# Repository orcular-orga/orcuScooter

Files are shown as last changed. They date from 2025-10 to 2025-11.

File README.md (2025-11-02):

# orcuScooter

## 🛴♻️ Open Source Circular Scooter

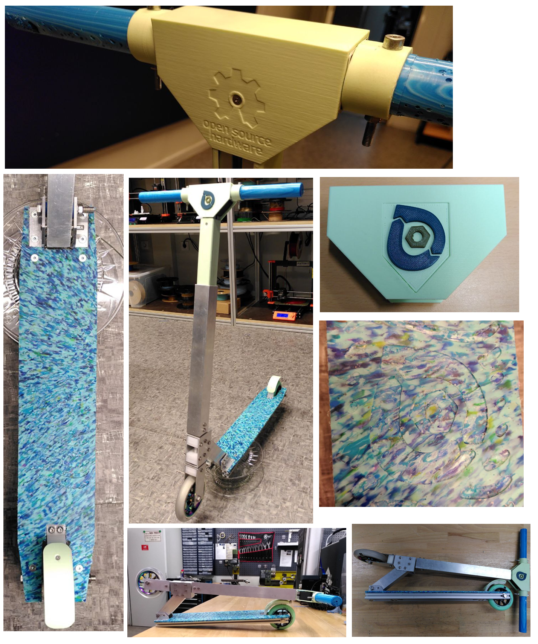
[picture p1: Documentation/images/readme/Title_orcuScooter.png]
 

The orcuScooter (short for "[Orcular](#%E2%84%B9%EF%B8%8F-about-the-orcular-project) Scooter") is an open-source kick scooter made from recycled plastics, aluminium and other parts. The main features are:
- Made from recycled plastics ([Precious Plastic](https://preciousplastic.com/) sheets)
- CNC milled parts
- 3D printed parts
- Circular design
  - Easy to repair & upgrade
  - Designed for disassembly
  - Most parts recyclebale
- [Open-source hardware](#-license)
- Designed in [FreeCAD](https://www.freecad.org/) (open-source software)
  - CAD file accessible in this repository
 
## 🏷️ Version
Recent version: 1.0 (released October 30th, 2025)

## 📐 CAD

This project has been designed in [FreeCAD](https://www.freecad.org/). You can find the CAD file [here](CAD)
 
## 🛠️ Building instructions
 
Here is all the information needed to manufacture and build an orcuScooter:

- 🛒 [Shopping list](Documentation/Shopping_list.md)
- ♻️ [Making sheets from recycled plastics](Documentation/Making_sheets.md)
- 🖨️ [3D printing](Documentation/3D_printing.md)
- ⚙️ CNC milling *(coming soon)*
- 🛠️ [Assembly](Documentation/Assembly.md)
- 🔼 Modding and upgrades *(coming soon)*

## 3D view

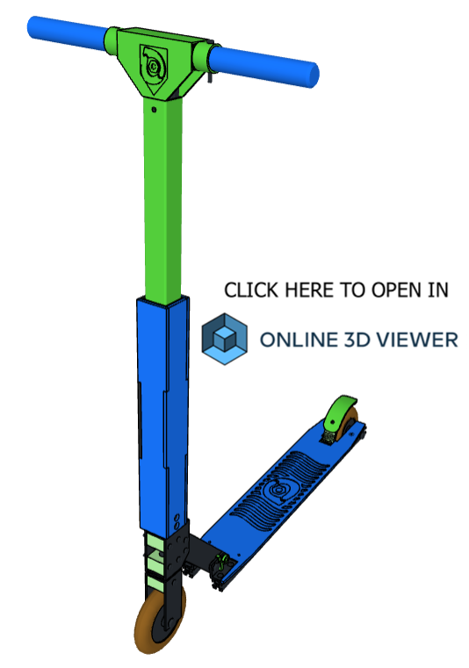
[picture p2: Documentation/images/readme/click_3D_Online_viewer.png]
[](https://3dviewer.net/embed.html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,-821.80037,1238.35295,82.32449,307.77471,405.61716,0.00000,-0.00000,1.00000,45.00000$projectionmode=perspective$envsettings=fishermans_bastion,off$backgroundcolor=255,255,255,255$defaultcolor=200,200,200$defaultlinecolor=100,100,100$edgesettings=on,0,0,0,84)

- It is best to open the view in a new tab (right-click on the image above -> Open link in new tab)
- Please be patient and wait about a minute to load the online 3D view

Controls:
- On computer: Use the left mouse button to rotate, the right mouse button to pan and the mouse wheel to zoom
- On smartphones: Swipe to rotate, use two fingers to zoom and pan 

- Alternative 3D view with more tools [here](https://3dviewer.net/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)
  - Click "Set Z axis as up vector" for better display a 
  - You can hide/show parts and groups on the left-hand side
  - For a complete view of the 3D file, download the [CAD file](CAD) and open it in [FreeCAD](https://www.freecad.org/)

## ℹ️ About the Orcular project
The orcuScooter is part of the Orcular project - https://www.orcular.org

"Orcular" stands for **O**pen Source + Ci**rcular** Economy

The project is about design concepts for locally recyclable products - for a constantly growing open source product library and the development of inner-city production.

Most components can be recycled into new parts - all within one city.
Recyclable plastic parts from the laser cutter, 3D printer and CNC mill, supplemented by standard parts.

## 📜🔓 License

The orcuScooter hardware design, CAD files, BOM, and relative files are released under the following open source license:

- [CERN Open Hardware Licence Version 2 Weakly Reciprocal - CERN-OHL-W](https://cern-ohl.web.cern.ch/)

The orcuScooter documentation, assembly manual, pictures and presentation text of this repository are released under the following license:

- [Creative-Commons-Attribution-ShareAlike 4.0 International - CC BY-SA 4.0](http://creativecommons.org/licenses/by-sa/4.0/)

**Author:** Oskar Lidtke, https://github.com/orcular-org/

<br />Except where otherwise noted, this work is licensed under a <a rel="license" href="http://creativecommons.org/licenses/by-sa/4.0/">Creative Commons Attribution-ShareAlike 4.0 International License (CC BY-SA 4.0)</a>.

See best practices for [attribution](https://wiki.creativecommons.org/wiki/Best_practices_for_attribution) and [marking your own work](https://wiki.creativecommons.org/wiki/Marking_your_work_with_a_CC_license) with a CC license.

<p align="left">
<i> <sub> Open Source Hardware logo, <a href="https://creativecommons.org/licenses/by-sa/4.0/">CC BY-SA</a> - <a href="https://oshwa.org/resources/open-source-hardware-logo/">Source</a> </sub></i>
</p>



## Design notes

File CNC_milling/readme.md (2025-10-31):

This folder contains the CNC milling vector graphics files. For CNC milling instructions, see the [documentation](../Documentation/Introduction.md), section **CNC milling**.

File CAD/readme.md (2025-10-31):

**Recent version: 1.0** - released on October 30, 2025.

The CAD model was designed in FreeCAD. You can download this free and open-source software on https://www.freecad.org

For modding instructions and changing parameters in the CAD file, see the [documentation](../Documentation/Introduction.md), section **Modding and upgrades**.

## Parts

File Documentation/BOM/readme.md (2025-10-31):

BOM / Shopping list

Can also be found here: [Google Docs Link](https://docs.google.com/spreadsheets/d/1hvMtBMdU-MjT3f36fKkWHgp-UORz1duzvwJJqe4S46w/edit?usp=drive_link)

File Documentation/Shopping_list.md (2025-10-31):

# Shopping list + bill of materials (BOM)

The shopping list / BOM can be found here [Google Docs Link](https://docs.google.com/spreadsheets/d/1hvMtBMdU-MjT3f36fKkWHgp-UORz1duzvwJJqe4S46w/edit?usp=drive_link)
or can be downloaded here: [Download BOM](BOM)

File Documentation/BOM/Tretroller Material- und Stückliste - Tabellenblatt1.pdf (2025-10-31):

## 🛠 Material- und Stückliste

Für einen (1)
Tretroller- Prototypen

Für zwei (2)
Prototypen
+ Puffer
Funktion | Material / Bauteil | Maße | Menge

Benötigte
Menge

Stück / Verkaufseinh.

Verkaufseinh.
bestellen | Link
🔲 Aluminium-Vierkantprofile, -Winkel und -Rundstäbe | L = 130 , da die Mindestlänge 50 mm beträgt, also 40 mm nicht möglich --> 130 mm bestellen und auseinandersägen
Fork | Vierkantprofil | 100x40x3 L=40 | 1 | 1 | https://www.metallparadies.de/alu-vierkantrohr.html
Bearing Box | Vierkantprofil | 80x40x3 L=58 | 1 | 2 | https://www.metallparadies.de/alu-vierkantrohr.html
Cross Connection | Vierkantprofil | 40x30x4 L=190 | 1 | 2 | https://www.metallparadies.de/alu-vierkantrohr.html
Gehrungswinkel: 45 ° und 38 °
Axle | Rundstab | D=12 | L=147 | 1 | 2 | https://www.metallparadies.de/alu-vollrohr.html
Handle Bar Bottom | Vierkantprofil | 40x40x2 L=373 | 1 | 2 | https://www.metallparadies.de/alu-vierkantrohr.html
Angle | Winkel | 30x20x4 L=50 | 2 | 4 | https://www.metallparadies.de/aluwinkel.html
Bestellwert metallparadies | Warenwert | 72,77€
Versandkosten | 10,77€

### ✖ Konstruktionsprofile + Winkel + Nutensteine (Muttern für T-Nuten)

Handle Bar Top | Konstruktionsprofil | 30x30 L=364 | 1 | 2 | https://www.maunsystem.de/profil-6-30x30-natur/pi-3010-sz#ncfg=364
Handle Bar Horizontal | Konstruktionsprofil | 30x30 L=112 | 1 | 2 | https://www.maunsystem.de/profil-6-30x30-natur/pi-3010-sz#ncfg=112
Frame Base | Konstruktionsprofil | 20x20 L=504 | 2 | 4 | https://www.maunsystem.de/profil-5-20x20-natur/pi-4030-sz#ncfg=504
Frame Connectors | Konstruktionsprofil | 20x20 L=41 | 2 | 4 | https://www.maunsystem.de/profil-5-20x20-natur/pi-4030-sz#ncfg=41
Frame | Winkelsatz 20 x 20 | | | 4 | 8 | https://www.maunsystem.de/winkelsatz-5-20x20/zi-4040
Handle Bar Top | Winkelsatz 30 x 30 | | | 2 | 4 | https://www.maunsystem.de/winkelsatz-6-30x30/zi-3070
Handle Bar Top <-> Flügelschraube | Nutenstein | M5 | | 1 | 2 | https://www.maunsystem.de/nutenstein-5-st-m5-verzinkt/ni-4035
Handle Bar Top <-> Begrenzung | Nutenstein | M5 | | 1 | 2 | https://www.maunsystem.de/nutenstein-5-st-m5-verzinkt/ni-4035
Bestellwert maunsystem | Warenwert | 134,18€
Versandkosten | 59,95€

### 🔩 Schrauben + Muttern + Unterlegscheiben

Hinweis: Alle Schrauben, Muttern, Unterlegscheiben möglichst aus Edelstahl, da Regen/Feuchtigkeit ausgesetzt (Korrosionsschutz) - Festigkeitsklasse A2 bevorzugt, da günstiger und ausreichende Festigkeit
Rear Wheel (Axle) | Sechskantschraube, Teilgewinde | M8 x 95 | 1 | https://www.schraubenking-shop.de/M8-x-95mm-Sechskantschrauben-DIN931-Teilgewinde-Edelstahl-A2-P005472
| Mutter | M8 | 1 | https://www.schraubenking-shop.de/M8-Sechskantmuttern-DIN934-Edelstahl-A2-P000451
| Unterlegscheibe (Außen-D = 20) | M8 | 2 | https://www.schraubenking-shop.de/84-x-20mm-Kotfluegelscheiben-Edelstahl-A2-P009141
Angle <-> Frame | Senkkopfschraube | M5 x 30 | 4 | https://www.schraubenking-shop.de/M5-x-30mm-Senkschrauben-ISO10642-Edelstahl-A2-P001361
| Mutter | M5 | 4 | https://www.schraubenking-shop.de/M5-Sechskantmuttern-DIN934-Edelstahl-A2-P000449
| Unterlegscheibe (Außen-D = 20) | M5 | 4 | https://www.schraubenking-shop.de/53-x-20mm-Kotfluegelscheiben-Edelstahl-A2-P008767
Angle <-> Cross Connection | Sechskantschraube, Teilgewinde | M8 x 65 | 1 | https://www.schraubenking-shop.de/M8-x-65mm-Sechskantschrauben-DIN931-Teilgewinde-Edelstahl-A2-P002677
| Mutter | M8 | 1 | https://www.schraubenking-shop.de/M8-Sechskantmuttern-DIN934-Edelstahl-A2-P000451
| Unterlegscheibe | M8 | 2 | https://www.schraubenking-shop.de/84mm-Unterlegscheiben-DIN125-Edelstahl-A2-P000475
Bearing Box <-> Cross Connection | Sechskantschraube, Teilgewinde | M5 x 50 | 2 | https://www.schraubenking-shop.de/M5-x-50mm-Sechskantschrauben-DIN931-Teilgewinde-Edelstahl-A2-P000277
| Mutter | M5 | 2 | https://www.schraubenking-shop.de/M5-Sechskantmuttern-DIN934-Edelstahl-A2-P000449
| Unterlegscheibe | M5 | 4 | https://www.schraubenking-shop.de/53mm-Unterlegscheiben-DIN125-Edelstahl-A2-P000036
Bearing Box <-> Bearing Housing | Sechskantschraube, Teilgewinde | M5 x 50 | 4 | https://www.schraubenking-shop.de/M5-x-50mm-Sechskantschrauben-DIN931-Teilgewinde-Edelstahl-A2-P000277
| Mutter | M5 | 4 | https://www.schraubenking-shop.de/M5-Sechskantmuttern-DIN934-Edelstahl-A2-P000449
| Unterlegscheibe | M5 | 8 | https://www.schraubenking-shop.de/53mm-Unterlegscheiben-DIN125-Edelstahl-A2-P000036
Fork <-> Axle | Sechskantschraube, Teilgewinde | M5 x 50 | 1 | https://www.schraubenking-shop.de/M5-x-50mm-Sechskantschrauben-DIN931-Teilgewinde-Edelstahl-A2-P000277
| Mutter | M5 | 1 | https://www.schraubenking-shop.de/M5-Sechskantmuttern-DIN934-Edelstahl-A2-P000449
| Unterlegscheibe | M5 | 2 | https://www.schraubenking-shop.de/53mm-Unterlegscheiben-DIN125-Edelstahl-A2-P000036
Front Wheel (Axle) | Sechskantschraube, Teilgewinde | M8 x 50 | 1 | https://www.schraubenking-shop.de/M8-x-50mm-Sechskantschrauben-DIN931-Teilgewinde-Edelstahl-A2-P005469
| Mutter | M8 | 1 | https://www.schraubenking-shop.de/M8-Sechskantmuttern-DIN934-Edelstahl-A2-P000451
| Unterlegscheibe | M8 | 2 | https://www.schraubenking-shop.de/84mm-Unterlegscheiben-DIN125-Edelstahl-A2-P000475
Handle Bar Bottom <-> Axle (+ Nylonschiene) | Sechskantschraube, Teilgewinde | M5 x 50 | 3 | https://www.schraubenking-shop.de/M5-x-50mm-Sechskantschrauben-DIN931-Teilgewinde-Edelstahl-A2-P000277

| Mutter | M5 | 3 | | | | | https://www.schraubenking-shop.de/M5-Sechskantmuttern-DIN934-Edelstahl-A2-P000449
| Unterlegscheibe | M5 | 4 | | | | | https://www.schraubenking-shop.de/53mm-Unterlegscheiben-DIN125-Edelstahl-A2-P000036
Arretierung höhenverstellbarer Lenker | Flügelschraube | M5 x 16 | 1 | | | | | https://www.schraubenking-shop.de/M5-x-16mm-Fluegelschrauben-amerik-Form-Edelstahl-A2-P005164
Schraube f. Nutenstein Begrenzung Lenkstange Linsenflachkopfschraube | M5 x 10 | 1 | https://www.schraubenking-shop.de/M5-x-10mm-Linsenflachkopfschraube-ISK-ISO7380-Edelstahl-A2-P004443
Begrenzung Nylonschiene oben + für Inserts | Senkschraube | M3 x 12 | 8 | | | | | https://www.schraubenking-shop.de/M3-x-12mm-Senkschrauben-ISO10642-Edelstahl-A2-P002506
| Mutter | M3 | 2 | | | | | https://www.schraubenking-shop.de/M3-Sechskantmuttern-DIN934-Edelstahl-A2-P000447

Sortiert nach Teiletyp:

Schrauben

Benötigte
Menge
| | | | | Stück / Verkaufseinh. | Verkaufseinh.
bestellen | Warenkorb
Rear Wheel (Axle) | Sechskantschraube, Teilgewinde | M8 x 95 | 1 | 2 | 1 | 2 | x | https://www.schraubenking-shop.de/M8-x-95mm-Sechskantschrauben-DIN931-Teilgewinde-Edelstahl-A2-P005472
Angle <-> Frame | Senkkopfschraube | M5 x 30 | 4 | 8 | 10 | 1 | x | https://www.schraubenking-shop.de/M5-x-30mm-Senkschrauben-ISO10642-Edelstahl-A2-P001361
Angle <-> Cross Connection | Sechskantschraube, Teilgewinde | M8 x 65 | 1 | 2 | 1 | 2 | x | https://www.schraubenking-shop.de/M8-x-65mm-Sechskantschrauben-DIN931-Teilgewinde-Edelstahl-A2-P002677
Bearing Box <-> Cross Connection | Sechskantschraube, Teilgewinde | M5 x 50 | 2 | 4 | | | | https://www.schraubenking-shop.de/M5-x-50mm-Sechskantschrauben-DIN931-Teilgewinde-Edelstahl-A2-P000277
Bearing Box <-> Bearing Housing | Sechskantschraube, Teilgewinde | M5 x 50 | 4 | 8 | | | | https://www.schraubenking-shop.de/M5-x-50mm-Sechskantschrauben-DIN931-Teilgewinde-Edelstahl-A2-P000277
Fork <-> Axle | Sechskantschraube, Teilgewinde | M5 x 50 | 1 | 2 | | | | https://www.schraubenking-shop.de/M5-x-50mm-Sechskantschrauben-DIN931-Teilgewinde-Edelstahl-A2-P000277
Handle Bar Bottom <-> Axle (+ Nylonschiene) | Sechskantschraube, Teilgewinde | M5 x 50 | 3 | 6 | | | | https://www.schraubenking-shop.de/M5-x-50mm-Sechskantschrauben-DIN931-Teilgewinde-Edelstahl-A2-P000277
Gesamt M5 x 50 | | | | 20 | 10 | 3 | x
Front Wheel (Axle) | Sechskantschraube, Teilgewinde | M8 x 50 | 1 | 2 | 1 | 2 | x | https://www.schraubenking-shop.de/M8-x-50mm-Sechskantschrauben-DIN931-Teilgewinde-Edelstahl-A2-P005469
Arretierung höhenverstellbarer Lenker | Flügelschraube | M5 x 16 | 1 | 2 | 1 | 2 | x | https://www.schraubenking-shop.de/M5-x-16mm-Fluegelschrauben-amerik-Form-Edelstahl-A2-P005164
Schraube f. Nutenstein Begrenzung Lenkstange Linsenflachkopfschraube | M5 x 10 | 1 | 2 | 10 | 1 | x | https://www.schraubenking-shop.de/M5-x-10mm-Linsenflachkopfschraube-ISK-ISO7380-Edelstahl-A2-P004443
Begrenzung Nylonschiene oben + für Inserts | Senkschraube | M3 x 12 | 8 | 16 | 100 | 1 | x | https://www.schraubenking-shop.de/M3-x-12mm-Senkschrauben-ISO10642-Edelstahl-A2-P002506

Muttern
| Mutter | M8 | 1 | 2 | | | | https://www.schraubenking-shop.de/M8-Sechskantmuttern-DIN934-Edelstahl-A2-P000451
| Mutter | M8 | 1 | 2 | | | | https://www.schraubenking-shop.de/M8-Sechskantmuttern-DIN934-Edelstahl-A2-P000451
| Mutter | M8 | 1 | 2 | | | | https://www.schraubenking-shop.de/M8-Sechskantmuttern-DIN934-Edelstahl-A2-P000451
Gesamt Muttern M8 | | | | 6 | 10 | 1 | x
| Mutter | M5 | 4 | 8 | | | | https://www.schraubenking-shop.de/M5-Sechskantmuttern-DIN934-Edelstahl-A2-P000449
| Mutter | M5 | 2 | 4 | | | | https://www.schraubenking-shop.de/M5-Sechskantmuttern-DIN934-Edelstahl-A2-P000449
| Mutter | M5 | 4 | 8 | | | | https://www.schraubenking-shop.de/M5-Sechskantmuttern-DIN934-Edelstahl-A2-P000449
| Mutter | M5 | 1 | 2 | | | | https://www.schraubenking-shop.de/M5-Sechskantmuttern-DIN934-Edelstahl-A2-P000449
| Mutter | M5 | 3 | 6 | | | | https://www.schraubenking-shop.de/M5-Sechskantmuttern-DIN934-Edelstahl-A2-P000449
Gesamt Muttern M5 | | | | 28 | 100 | 1 | x
Begrenzung Nylonschiene oben + für Inserts | Mutter | M3 | 2 | 4 | 100 | 1 | x | https://www.schraubenking-shop.de/M3-Sechskantmuttern-DIN934-Edelstahl-A2-P000447

Unterlegscheiben
| Unterlegscheibe (Außen-D = 20) | M8 | 2 | 4 | 10 | 1 | x | https://www.schraubenking-shop.de/84-x-20mm-Kotfluegelscheiben-Edelstahl-A2-P009141
| Unterlegscheibe (Außen-D = 20) | M5 | 4 | 8 | 10 | 1 | x | https://www.schraubenking-shop.de/53-x-20mm-Kotfluegelscheiben-Edelstahl-A2-P008767
| Unterlegscheibe (Außen-D = 16) | M8 | 2 | 4 | | | | https://www.schraubenking-shop.de/84mm-Unterlegscheiben-DIN125-Edelstahl-A2-P000475
| Unterlegscheibe (Außen-D = 16) | M8 | 2 | 4 | | | | https://www.schraubenking-shop.de/84mm-Unterlegscheiben-DIN125-Edelstahl-A2-P000475
Gesamt Unterlegscheibe M8 (Außen-D = 16) | | | | 8 | 100 | 1 | x
| Unterlegscheibe | M5 | 4 | 8 | | | | https://www.schraubenking-shop.de/53mm-Unterlegscheiben-DIN125-Edelstahl-A2-P000036
| Unterlegscheibe | M5 | 8 | 16 | | | | https://www.schraubenking-shop.de/53mm-Unterlegscheiben-DIN125-Edelstahl-A2-P000036
| Unterlegscheibe | M5 | 2 | 4 | | | | https://www.schraubenking-shop.de/53mm-Unterlegscheiben-DIN125-Edelstahl-A2-P000036
| Unterlegscheibe | M5 | 4 | 8 | | | | https://www.schraubenking-shop.de/53mm-Unterlegscheiben-DIN125-Edelstahl-A2-P000036

Gesamt Unterlegscheibe M5 | 36 | 100 | 1 | x
Bestellwert schraubenking | Warenwert | 18,38€
| Versandkosten | 5,90€

### ⚪🔩 Bolzen

Anlge <-> Cross Connection | Bolzen mit Kopf | 6 x 50 (6 x 48) | 1 | 3 | https://www.bootspunkt.de/steckbolzen-va-6x48-mm/ya-00-53102-0
Bestellwert bootspunkt | Warenwert | 2,55€
Versandkosten | 7,95€

### 🧵🔩 3D-Druck-Filament + Gewindeeinsätze zum Einschmelzen (Inserts)

| Nylon PA12 (750 g) | | 1 | 1 | https://www.reichelt.com/de/de/shop/produkt/filament_nylon_pa12_natural_1_75_mm_0_75_kg-405785
| PLA (1000 g) | | 1 | 1 | https://www.reichelt.de/de/de/shop/produkt/filament_panchroma_pla_matte_pastel_mint_1_75_mm_1_kg-405590
| Gewindeeinsatz zum Einschmelzen | M3 x 4 | 8 | 1 | https://www.reichelt.de/de/de/shop/produkt/3d_druck_gewindeeinsaetze_m3x4_short_100_stueck-332214
Bestellwert reichelt | Warenwert | 77,88€
Versandkosten | 5,95€

### 🍩 Kugellager

Lagerung Lenkachse | Schrägkugellager 7201 B offen TN | 12x32x10 mm | 2 | 4 | https://www.kugellager-express.de/schraegkugellager-7201-b-tn-offen-12x32x10-mm
Bestellwert kugellager-express | Warenwert | 18,61€
Versandkosten | 2,49€

### 🛒🛞 Kaufteile / Sonstige Teile

Front Wheel | Rolle | D=120 | 1 | 2 | https://angebot.decathlon.de/product/328632?modelId=8603756
Rear Wheel | Rolle | D=100 | 1 | 2 | https://angebot.decathlon.de/product/311734?modelId=8647663
Front + Rear Wheel (Eigenbau) | ABEC-5 Kugellager 2er Pack | | 2 | 2 | https://angebot.decathlon.de/product/312948?modelId=8575697
Bestellwert Decathlon | Warenwert | 75,94€
Versandkosten unbekannt
SUMME | 493,32 €

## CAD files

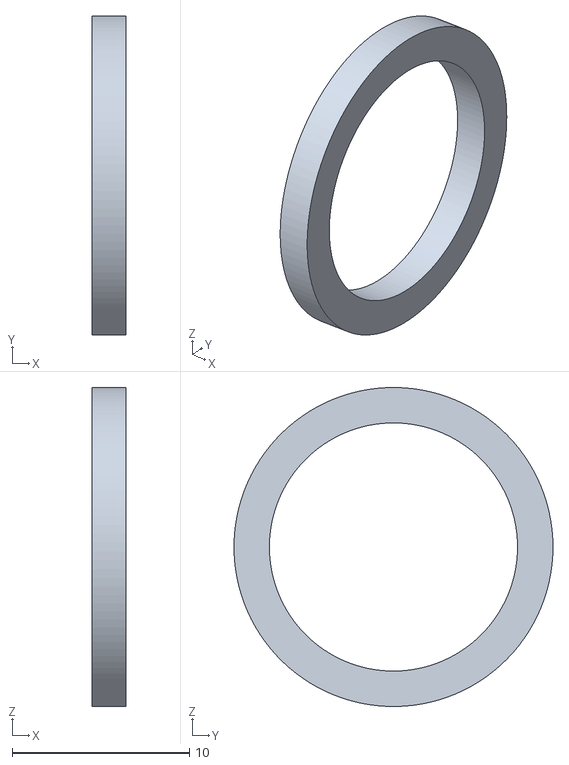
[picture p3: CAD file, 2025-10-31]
3D_printing/Nylon_(PA12)/3DP_Spacer_Cross_Connection_1,9.stl
1.90 x 18.0 x 18.0

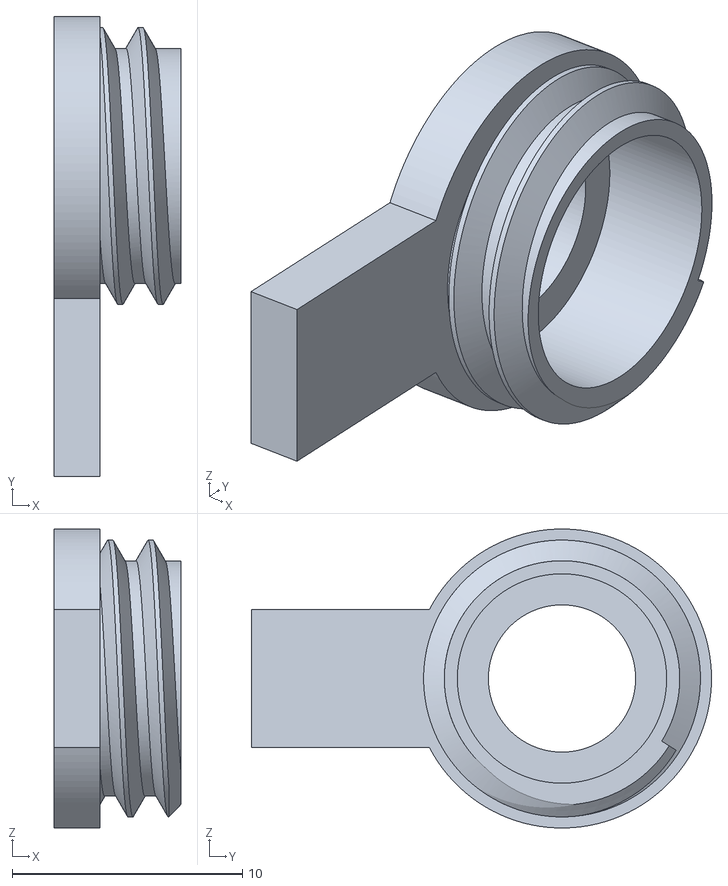
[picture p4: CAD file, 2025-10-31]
3D_printing/PLA/Cut.stl
5.50 x 20.0 x 13.0

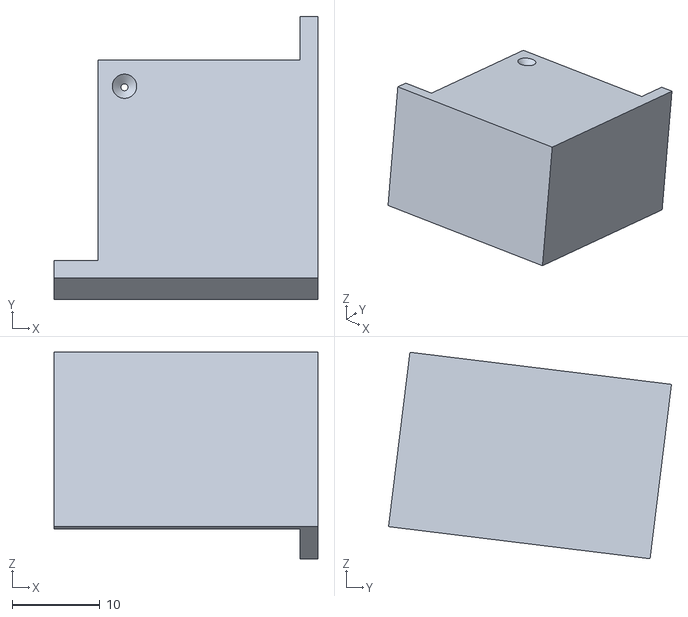
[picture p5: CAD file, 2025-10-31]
3D_printing/Templates_(PLA)/2-2_Drill_Guide.stl
30.0 x 32.2 x 23.5

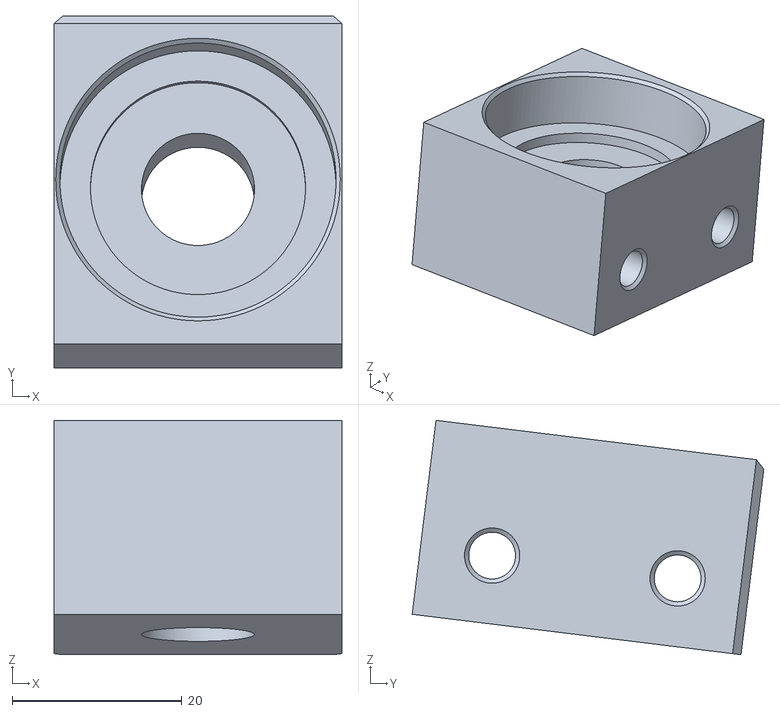
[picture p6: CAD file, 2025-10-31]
3D_printing/Nylon_(PA12)/3DP_Bearing_housing.stl
33.9 x 41.4 x 27.6

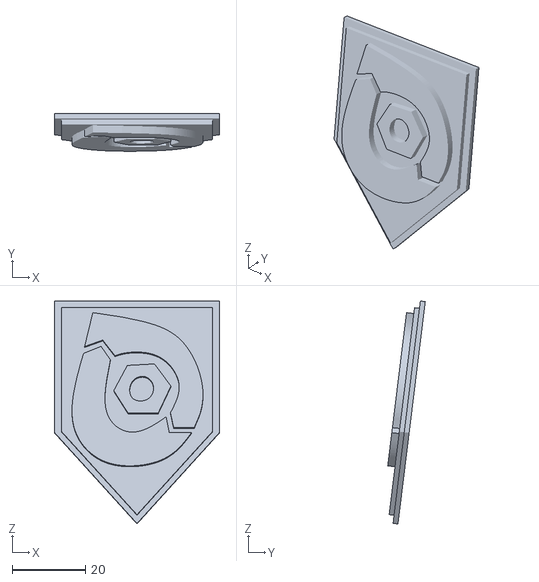
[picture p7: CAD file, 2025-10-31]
3D_printing/PLA/3DP_Logo_Orcular.stl
45.0 x 10.2 x 60.7

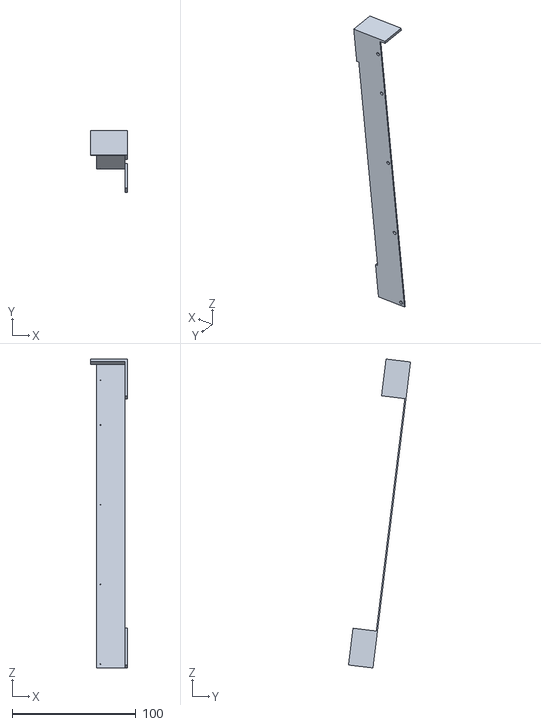
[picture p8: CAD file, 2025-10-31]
3D_printing/Templates_(PLA)/5-2_Drill_Guide.stl
30.0 x 50.3 x 250.1

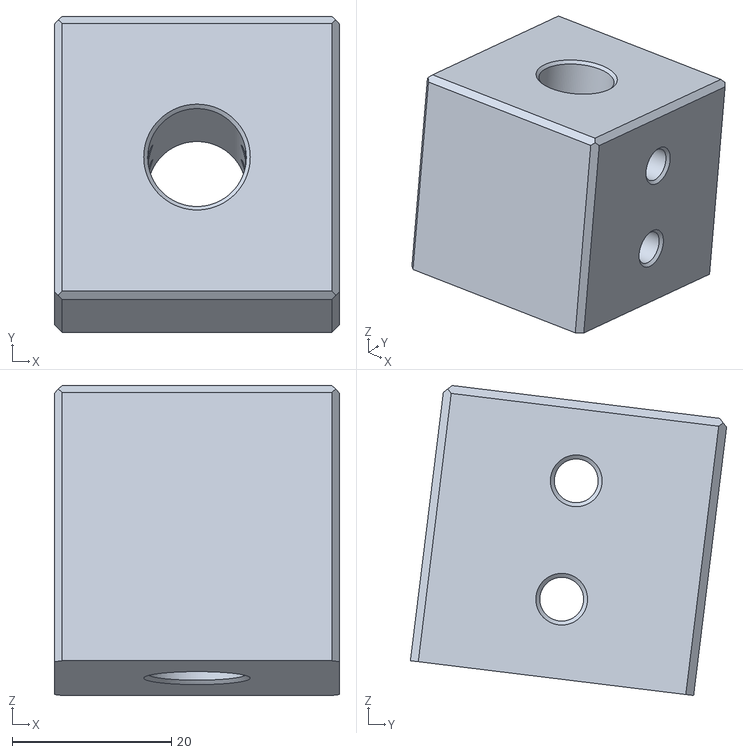
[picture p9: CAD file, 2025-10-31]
3D_printing/Nylon_(PA12)/3DP_Connector_Handle_Bar_Bottom+Axle.stl
35.9 x 39.8 x 39.0

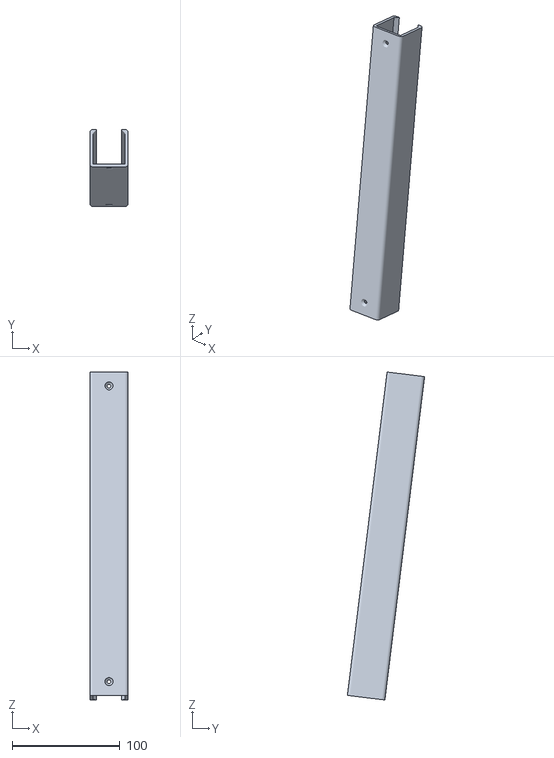
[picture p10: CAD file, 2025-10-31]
3D_printing/PLA/3DP_Case.stl
35.8 x 71.9 x 305.0

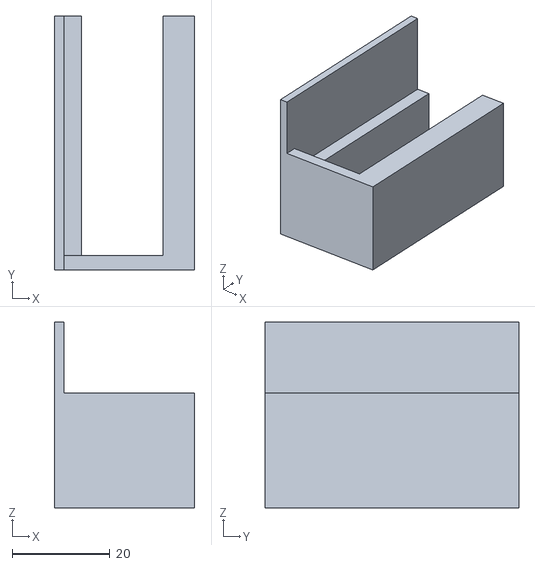
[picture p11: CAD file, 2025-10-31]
3D_printing/Templates_(PLA)/7-3_Drill_Guide.stl
28.7 x 52.0 x 38.0

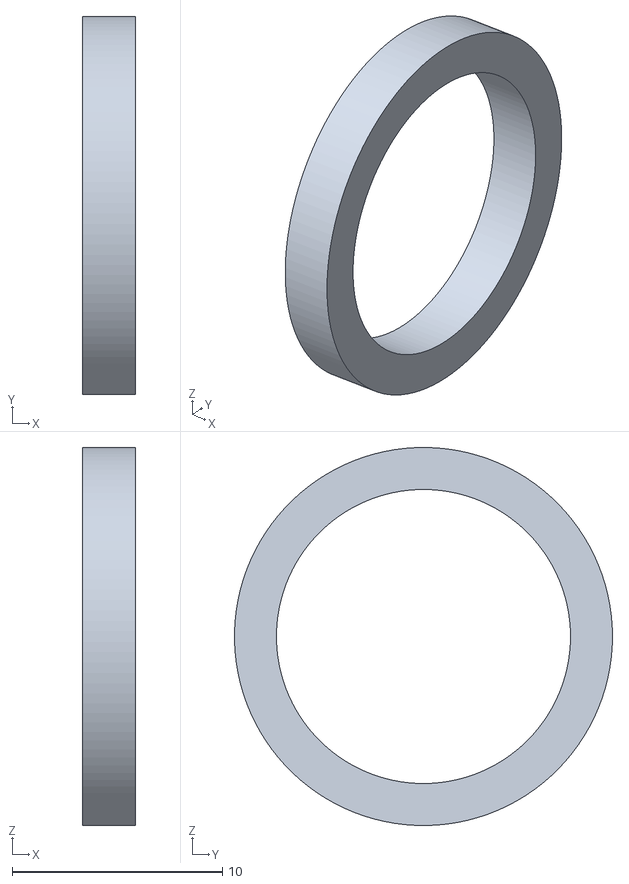
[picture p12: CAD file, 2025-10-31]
3D_printing/Nylon_(PA12)/3DP_Spacer_Cross_Connection_2,5.stl
2.50 x 18.0 x 18.0

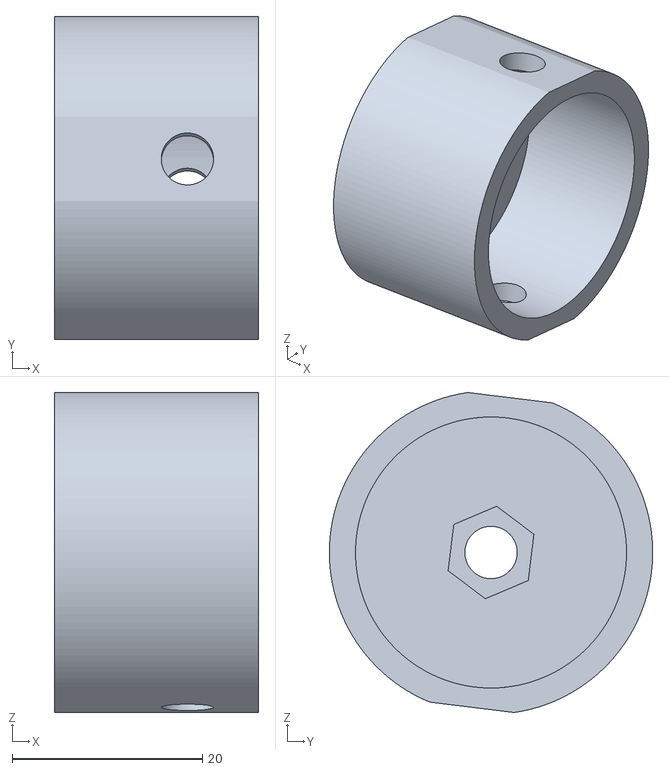
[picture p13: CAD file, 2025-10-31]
3D_printing/PLA/3DP_Handle_Adapter.stl
21.5 x 34.0 x 33.6

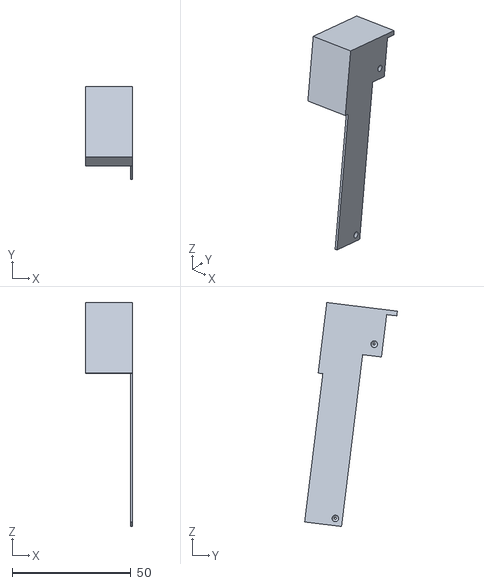
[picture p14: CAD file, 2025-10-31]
3D_printing/Templates_(PLA)/2-1_Drill_Guide.stl
20.0 x 39.1 x 94.5

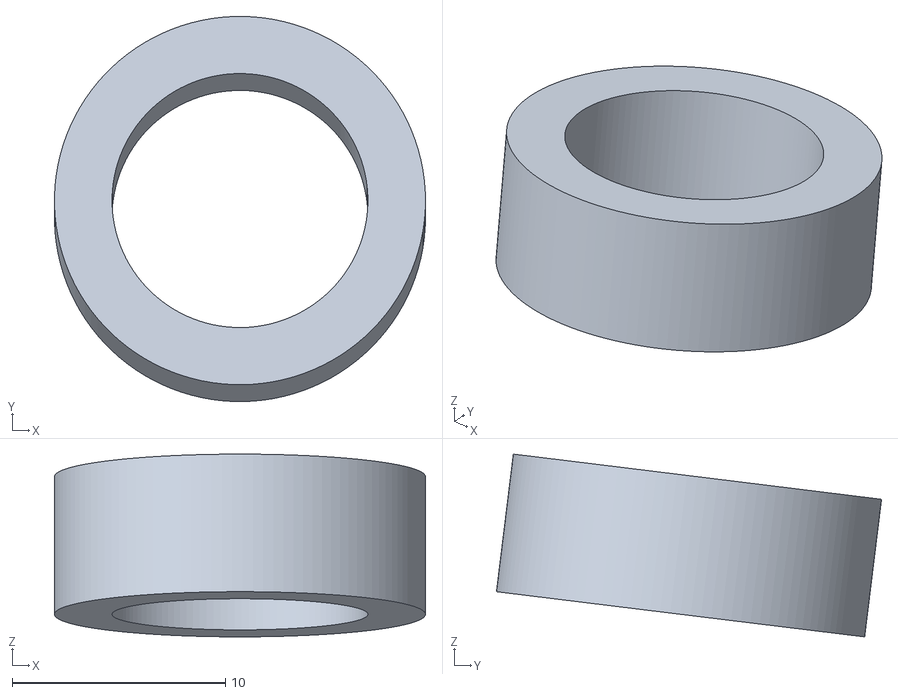
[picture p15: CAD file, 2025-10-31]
3D_printing/Nylon_(PA12)/3DP_Spacer_Handle_Bar_Bottom.stl
17.4 x 18.1 x 8.57

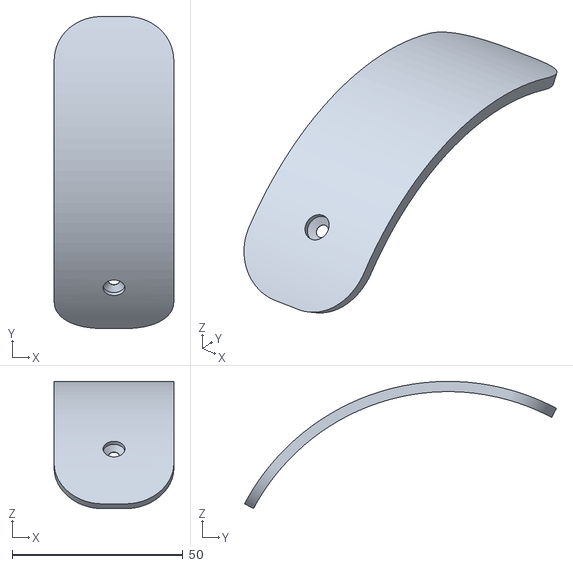
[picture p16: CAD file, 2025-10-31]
3D_printing/PLA/3DP_Brake_Cover.stl
35.0 x 91.3 x 37.2

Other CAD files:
3D_printing/Templates_(PLA)/7-2_Drill_Guide.stl
3D_printing/Nylon_(PA12)/3DP_Plain_bearing_rotation.stl
3D_printing/PLA/3DP_Front_Cover.stl
3D_printing/Templates_(PLA)/5-1_Drill_Guide.stl
3D_printing/Nylon_(PA12)/3DP_Brake.stl
3D_printing/Nylon_(PA12)/3DP_Connector_Fork.stl
3D_printing/Nylon_(PA12)/3DP_Nylon-Schiene.stl
3D_printing/Nylon_(PA12)/3DP_Spacer_Bearing_Box.stl
3D_printing/Nylon_(PA12)/3DP_Spacer_Fork.stl
3D_printing/Nylon_(PA12)/3DP_Spacer_Front_Wheel.stl
3D_printing/Nylon_(PA12)/3DP_Spacer_Rear_Wheel.stl
3D_printing/PLA/Deckel_real.stl
3D_printing/PLA/Klammer.stl
3D_printing/Templates_(PLA)/7-1a_Drill_Guide.stl
3D_printing/Templates_(PLA)/7-1b_Drill_Guide.stl
3D_printing/Templates_(PLA)/7-4_Drill_Guide.stl
3D_printing/Templates_(PLA)/7-5_Drill_Guide.stl

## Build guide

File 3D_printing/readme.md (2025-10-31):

This folder contains all 3D printing STL files. For printing instructions, see the [documentation](../Documentation/Introduction.md), section [3D printing](../Documentation/3D_printing.md).

You can click on any STL file to see a 3D view (GitHub feature).

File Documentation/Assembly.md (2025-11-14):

# Assembly

## Outline

💡ℹ️ You can find an outline (table of contents) in the upper right corner of this GitHub file and expand it by clicking on the icon. Click on the titles to jump to the corresponding section.

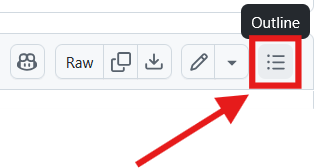
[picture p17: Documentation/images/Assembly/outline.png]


## Part list

Please check the part list in the [BOM section](Shopping_list.md)

## Tool list

Check that you have all the tools you need:

- A set of screw drivers and wrenches for hexagon screws (M3, M5 and M8)
- A set of allen keys
- Pliers

## Assembly

The assembly instructions are divided into several modules. These do not necessarily have to be assembled in the order listed below. Several people can also work on different modules at the same time. At the end, all modules must be assembled together.

## 1. Frame

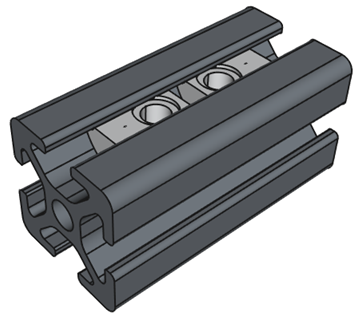
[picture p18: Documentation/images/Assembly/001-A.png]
<table> <tr> <td>  </td> <td> <ul>
        <li>Insert 2 t-nuts (M5) in one of the t-slot profiles (length 41 mm). You will need them later to assemble the brake.</li>
</table>

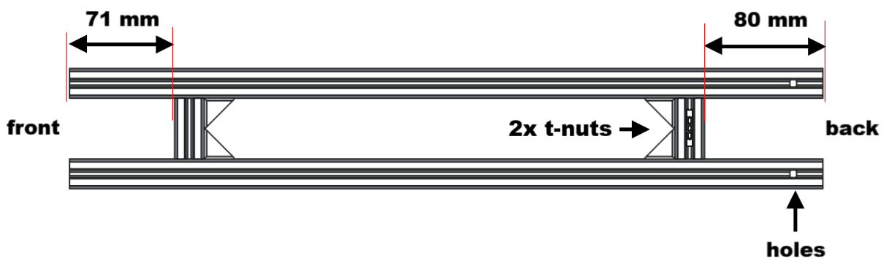
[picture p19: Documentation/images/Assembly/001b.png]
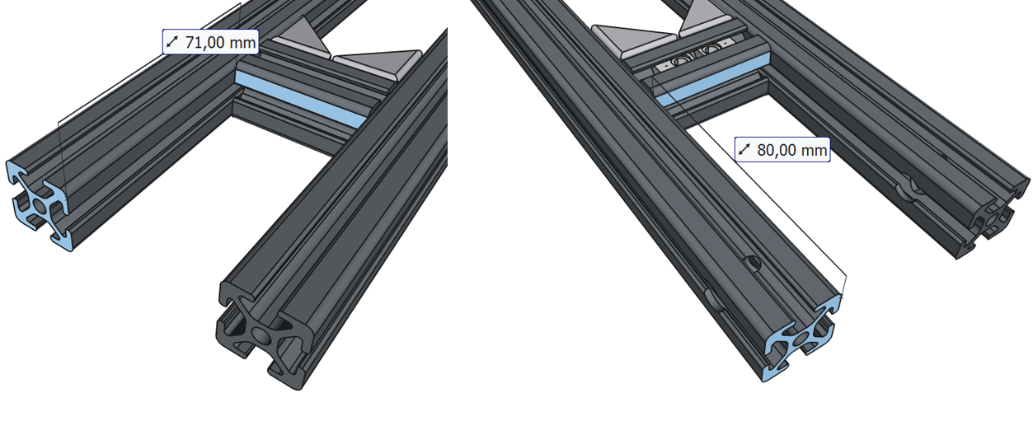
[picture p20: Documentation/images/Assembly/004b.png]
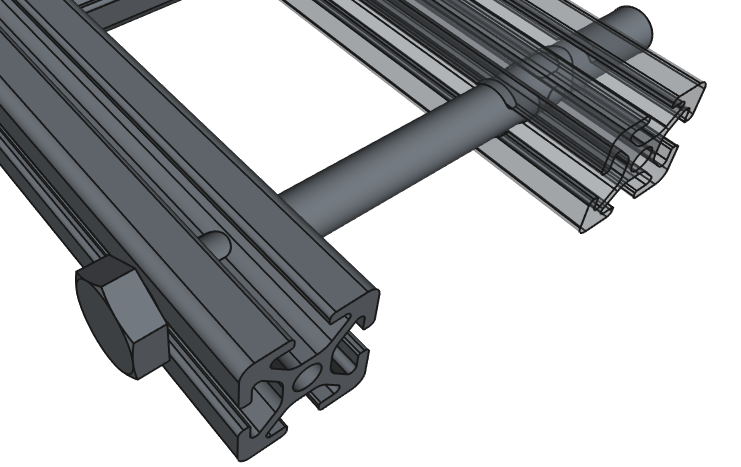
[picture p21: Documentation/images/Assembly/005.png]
<table> <tr> <td>  <br>  <br> </td> <td> <ul>
        <li>Assamble the following 20x20 t-slot profiles:
          <ul>
            <li>length 509 mm (2 pieces)</li>
            <li>length 41 mm (2 pieces)</li>
          </ul>
        </li>
        <li>Use four 20x20 angles for mounting</li>
        <li>For each angle, you will need 2x M5 screws and 2x t-nuts</li>
        <li>Make sure to move the 41-mm-profiles to the right position (80 mm for the back part, 71 mm for the front part)</li>
        <li>Make sure to put the part with the 2 t-nuts (for the brake) in the back part of the frame (with a distance 80 mm)</li>
        <li>Make sure that the drilled holes are in the back</li>
        <li>Make sure that everything is parallel and at right angles</li>
        <li>Insert the M8 x 95 screw through the holes and make sure that it fits well</li>
        <li>Do not fasten the screw yet. If the screw fits, remove it again. The rear wheel will be mounted later.</li>
      </ul> </td> </tr> </table>

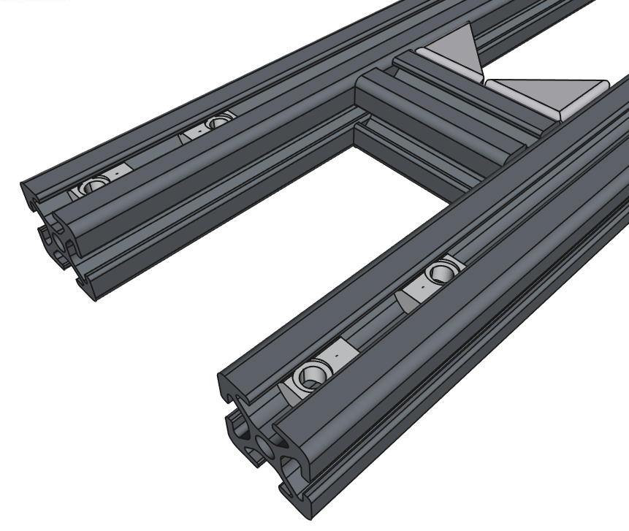
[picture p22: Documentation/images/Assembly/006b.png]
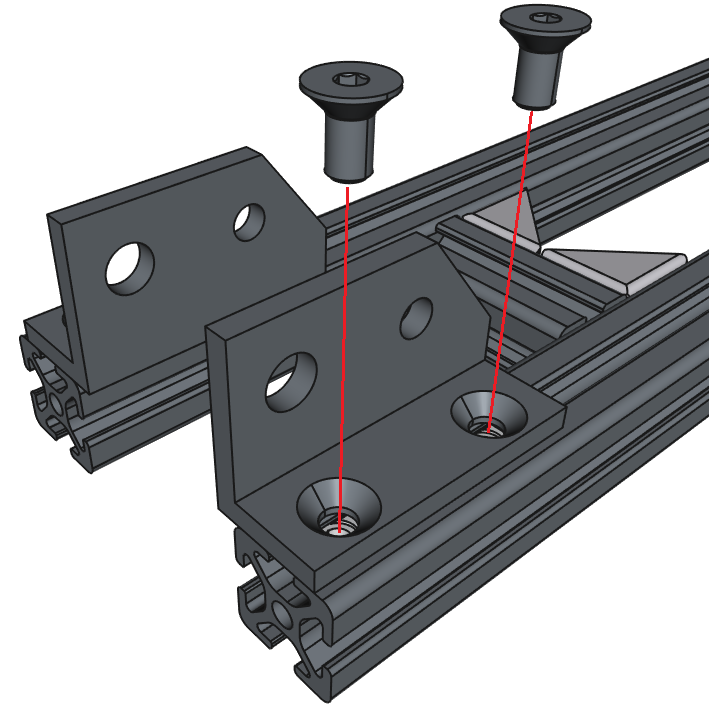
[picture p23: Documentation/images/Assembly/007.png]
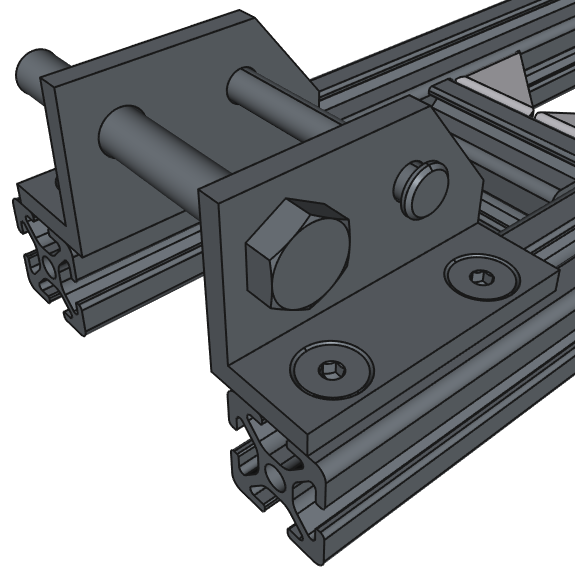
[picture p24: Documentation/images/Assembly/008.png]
<table> <tr> <td>  <br>  <br>  </td> <td> <ul>
        <li>Insert 4x t-nuts (with M5 holes) in the frame (2 on each side)</li>
        <li>Insert them on the front part of the frame (where the distance of the profile is 71 mm and where are no holes)</li>
        <li>Mount the two angles using 2x M5 x 10 countersunk screws for each part</li>
        <li>Ensure that the angles are flush with the profiles</li>
        <li>Insert the M8 x 65 screw through the bigger hole and the bolt through the smaller hole and make sure everything fits well</li>
        <li>Do not fasten the screw and the bolt yet. If the screw and the bolt fit, remove them again. These parts will be mounted later</li>
</table>

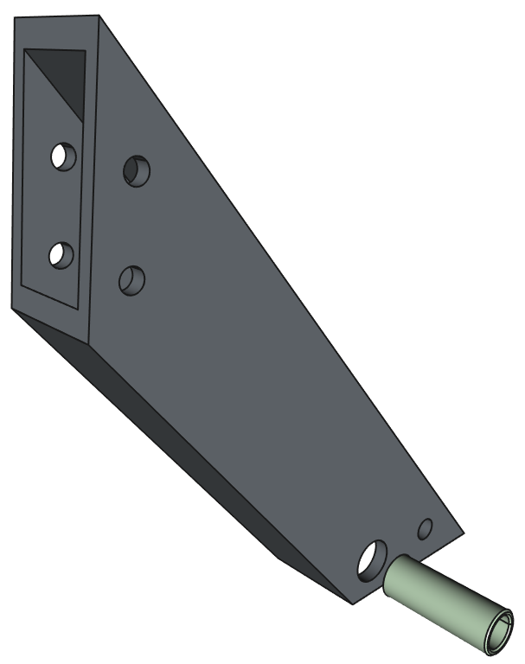
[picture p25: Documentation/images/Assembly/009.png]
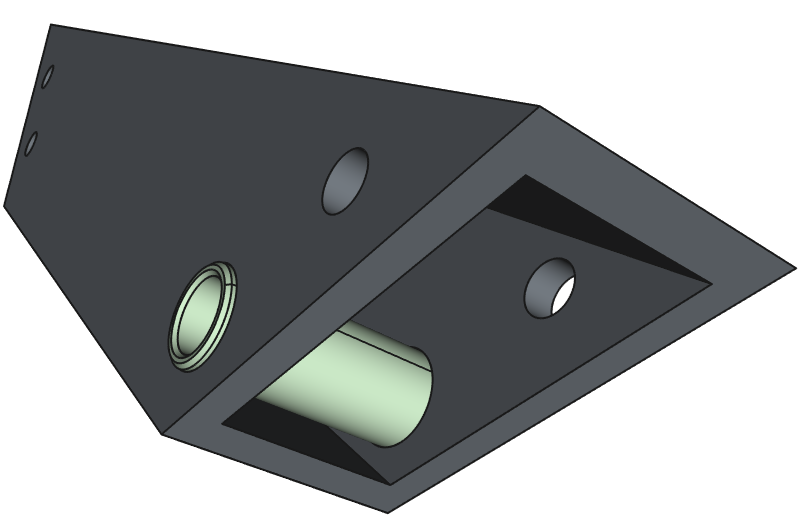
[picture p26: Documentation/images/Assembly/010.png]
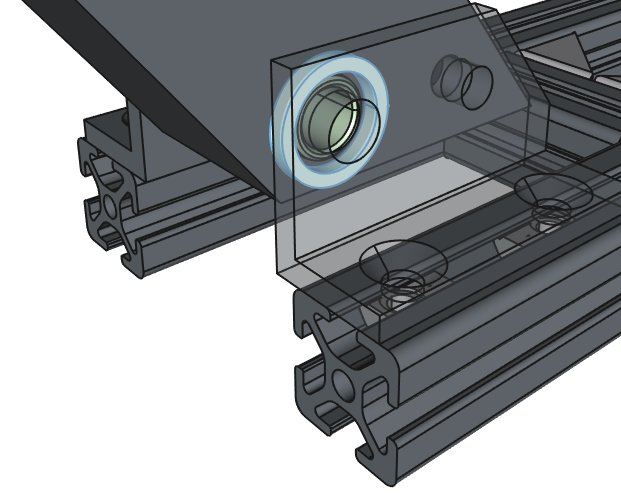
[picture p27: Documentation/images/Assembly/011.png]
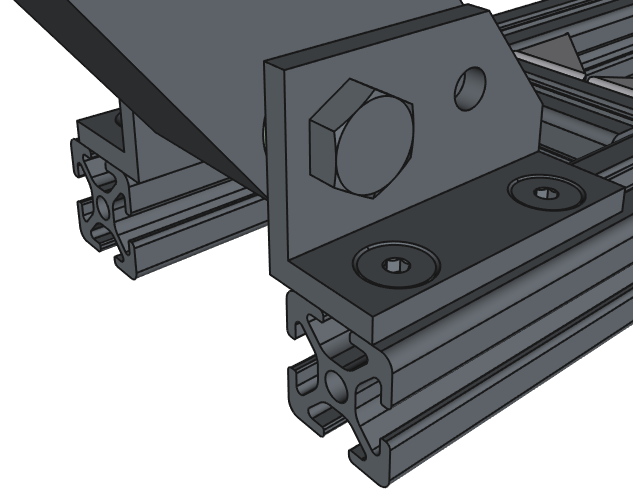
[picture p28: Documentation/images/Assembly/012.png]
<table> <tr> <td>  <br>  <br>  <br> </td> <td> <ul>
        <li>Insert the 3D-printed (nylon) plain bearing in the largest hole of the cross connection. It should sit tightly inside the hole.</li>
        <li>Mount the cross connection between the angles, using two 3D-printed spacers (18 x 2,5 or 18 x 1,9) and an M8 x 65 screw with washers on each side (washers not shown in the image)</li>
        <li>Try the 18 x 2,5 spacers first. If they don't fit, try the 18 x 1,9 ones. If none of them fit, edit the file in FreeCAD or in a slicer software and print spacers that fit well. The cross connection part should not wobble</li>
        <li>Tighten the screw with an M8 nut (not shown in the image)</li>
        <li>Test the connection. The part should be rotatable.</li>
</table>

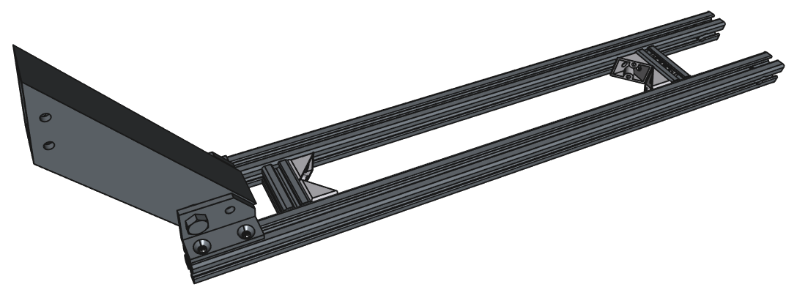
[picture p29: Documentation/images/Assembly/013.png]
<table> <tr> <td>  </td> <td> <ul>
        <li>The frame is now fully assembled. Set it aside and continue with the assembly of the other modules.</li>
</table>

## 2. Front wheel and fork

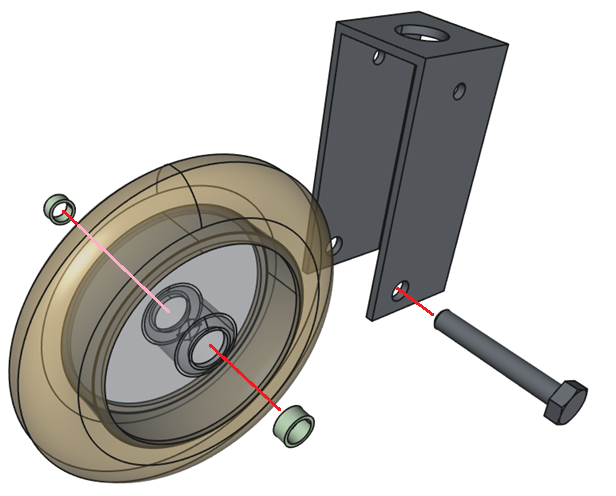
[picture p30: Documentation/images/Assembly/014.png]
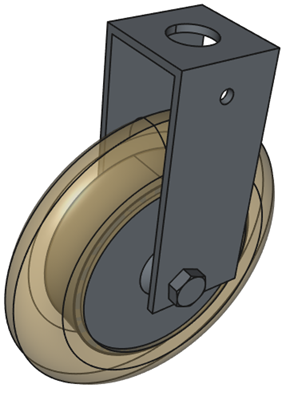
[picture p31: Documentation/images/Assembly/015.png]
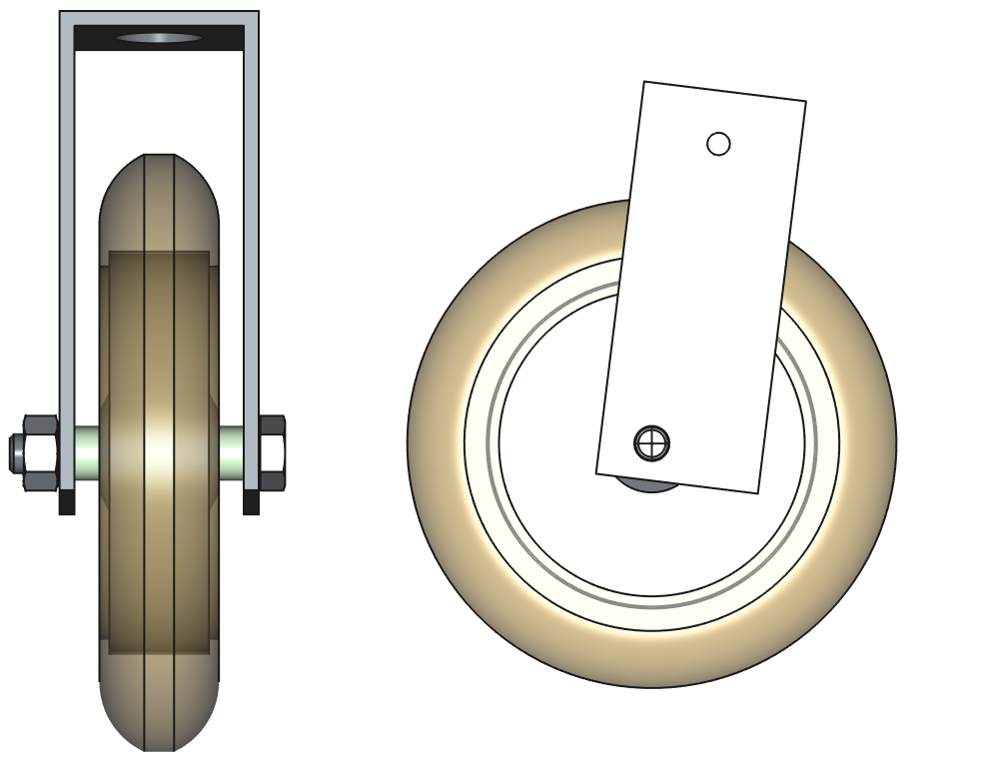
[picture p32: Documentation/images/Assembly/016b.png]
<table> <tr> <td>  <br>  <br>  </td> <td> <ul>
        <li>Prepare the following parts
                <ul>
                        <li>Fork</li>
                        <li>Front wheel (diameter 120 mm)</li>
                        <li>2x 3D-printed spacers (11 x 5 mm)</li>
                        <li>M8 x 50 screw</li>
                        <li>M8 nut (only shown in the third image)</li>
                        <li>2x washers (not shown in the images)</li>
                </ul>
        </li>
        <li>Have a pair of pliers ready that are narrow enough to insert the spacers.</li>
        <li>Put a washer on the screw</li>
        <li>Insert the screw through the hole (just a few millimeters beyond the hole)</li>
        <li>Put one of the spacers on the tip of the screw</li>
        <li>Hold the wheel and the other spacer (using the pliers) in position, then push the screw all the way through</li>
        <li>Put the second washer on the end of the screw and fasten it with an M8 nut</li>
        <li>Test the assembly. Make sure the wheel spins well and that it doesn't wobble.</li>
</table>

## 3. Handlebar (top part)

<table> <tr> <td>
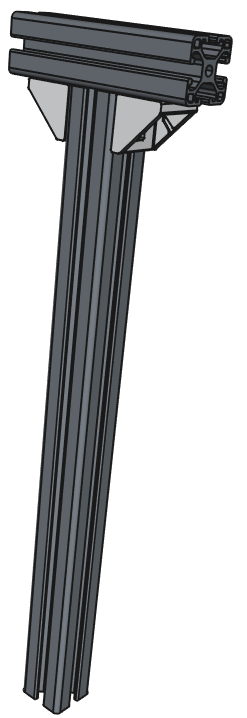
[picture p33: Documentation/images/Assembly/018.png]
         <br> 
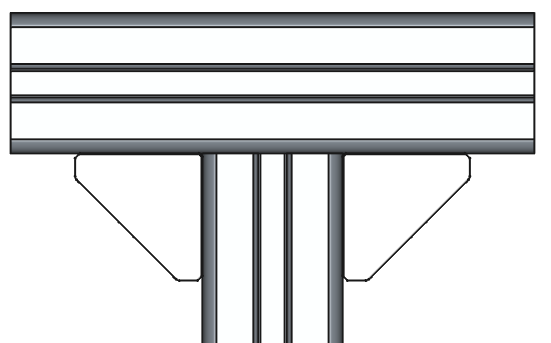
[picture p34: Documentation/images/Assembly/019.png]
         <br> 
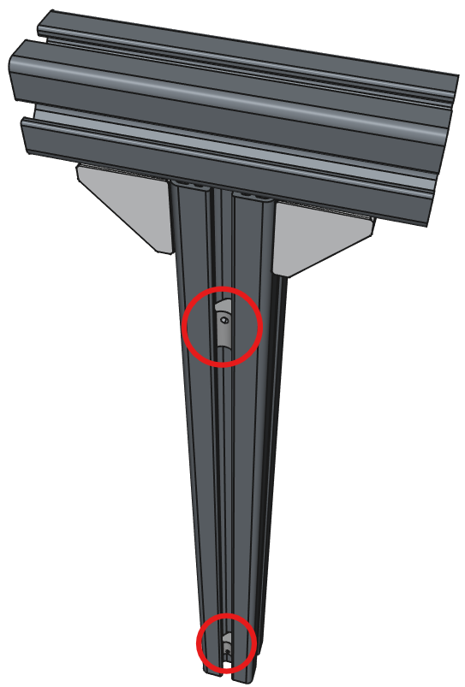
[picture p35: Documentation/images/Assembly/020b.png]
         <br> 
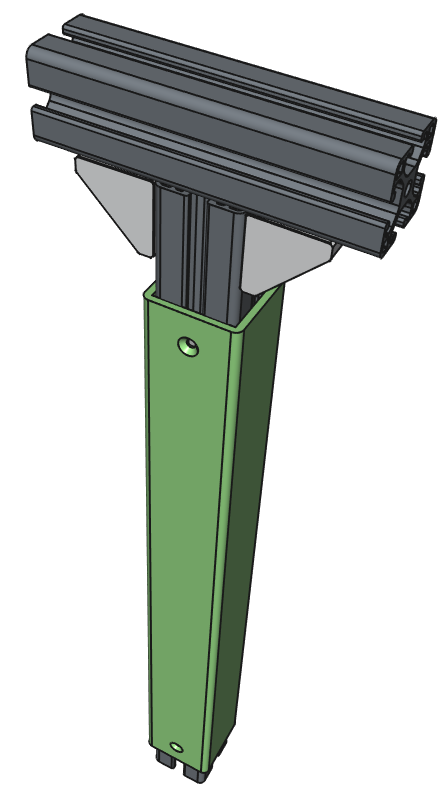
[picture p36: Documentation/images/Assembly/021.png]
        
</td> <td> <ul>
        <li>Assemble the two 30x30 profiles together (lenght 364 and 112 mm)</li>
        <li>Use two 30x30 angles for mounting</li>
        <li>For each angle, you will need 2x M5 screws and 2x t-nuts</li>
        <li>Make sure that the short profile on the top is centered</li>
        <li>If available, insert a cover cap on each angle (not shown in the images, not necessary, only for appearance)</li>
        <li>Insert two t-nuts (M3) in the front part of the long profile (red circles ⭕ in the image)</li>
        <li>Mount the 3D-printed case, using two M3 x 12 countersunk screws (screw them into the t-nuts)</li>
</table>

<table> <tr> <td>
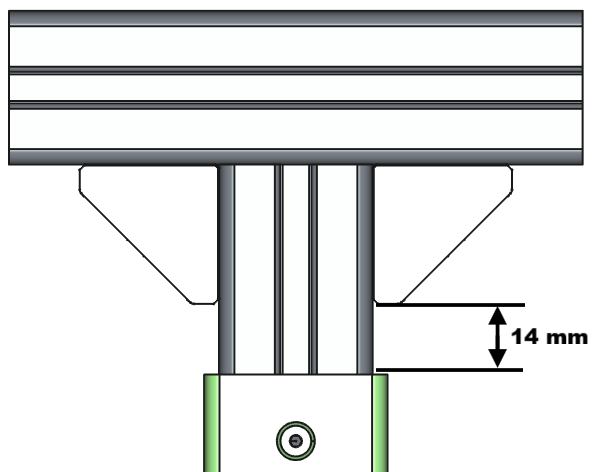
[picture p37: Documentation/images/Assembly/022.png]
         <br> 
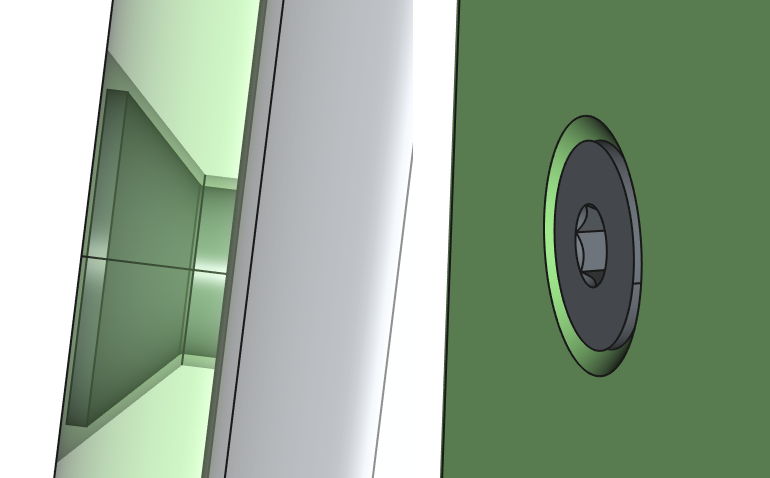
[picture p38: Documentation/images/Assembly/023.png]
        
</td> <td> <ul>
        <li>The distance between the top edge of the 3D-printed case and the edge of the angle should be about 14 mm </li>
        <li>This is important, so the front cover will fit. You can correct the distance later when mounting the front cover.</li>
        <li>Ensure that the countersunk screws are well hidden below the surface of the cover <br> so that they do not scratch the inner wall of the aluminum square profile later on.</li>
</table>

## 4. Handlebar (bottom part)

<table> <tr> <td>
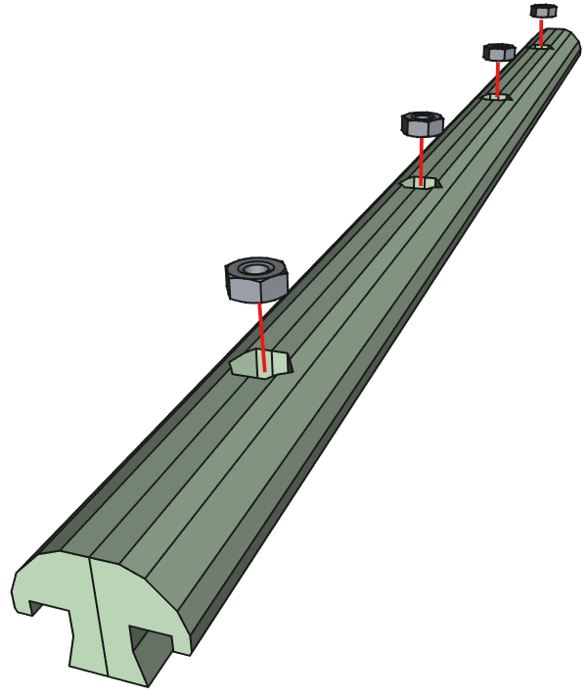
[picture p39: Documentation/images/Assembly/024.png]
         <br> 
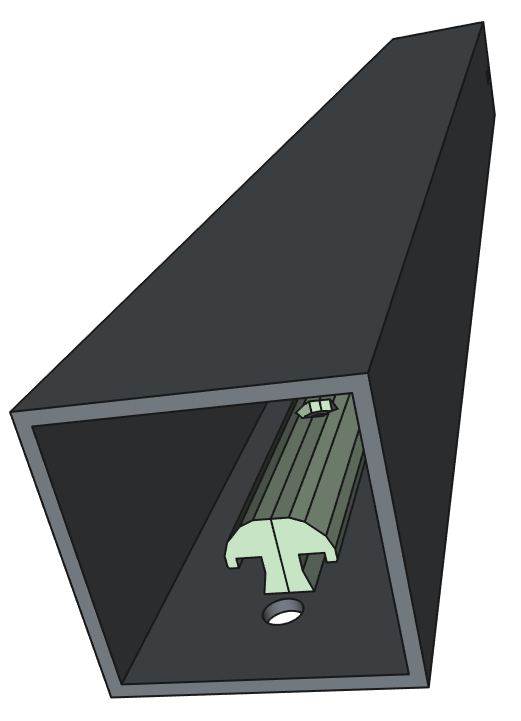
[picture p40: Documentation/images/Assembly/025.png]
         <br>
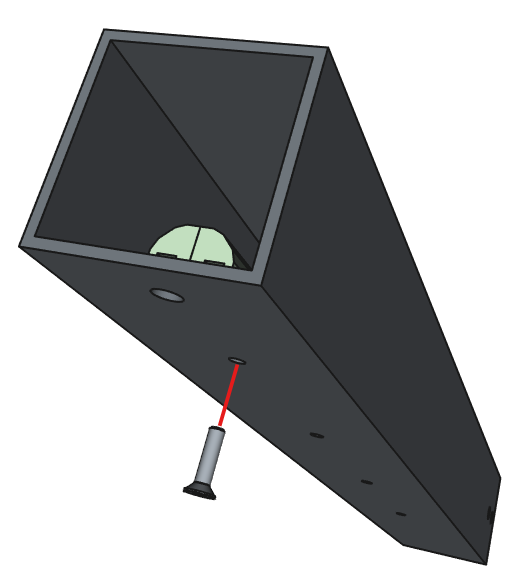
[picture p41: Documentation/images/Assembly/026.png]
         
</td> <td> <ul>
        <li>Insert four M3 nuts in the pockets of the nylon rail. Push them in as far as you can.</li>
        <li>Place the nylon rail with the M3 nuts inside the bottom part of the handlebar (40 x 40 mm aluminum square tube, length 373 mm)</li>
        <li>Align the 4 holes of the nylon rail with the 4 smaller holes in the square tube</li>
        <li>It might make assembly easier if you lay the square profile flat (as shown in the image)</li>
        <li>Use four M3 x 12 countersunk screws to attach the nylon rail inside the square tube (only one screw shown in the image)</li>
</table>

<table> <tr> <td>
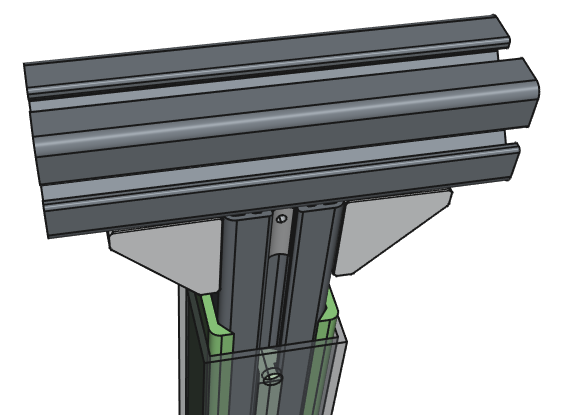
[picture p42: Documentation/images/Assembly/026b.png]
         <br> 
</td> <td> <ul>
        <li>It might make assembly easier if you insert the upper handlebar first so that it holds the nylon rail in position.</li>
</table>

<table> <tr> <td>
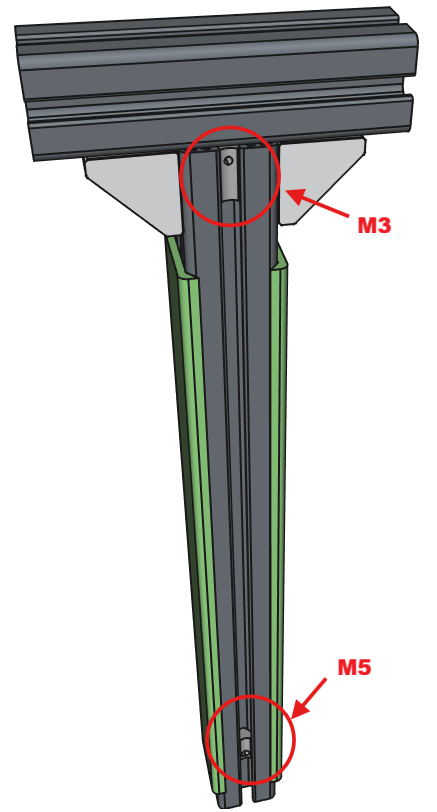
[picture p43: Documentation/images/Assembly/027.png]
         <br> 
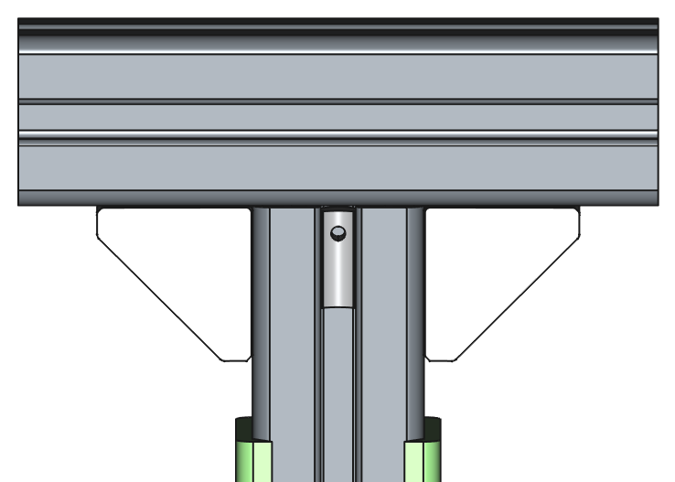
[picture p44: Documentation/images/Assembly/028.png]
         <br>
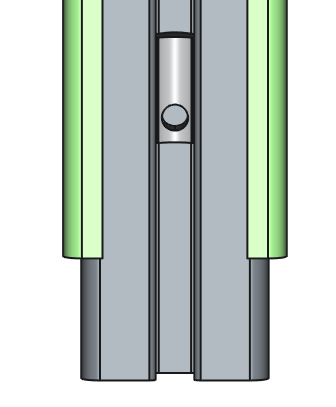
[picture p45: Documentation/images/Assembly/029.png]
         
</td> <td> <ul>
        <li>Insert a t-nut (M3) inside the t-slot profile of the handlebar (top part) and move it all the way to the top. You will need it later to assamble the front cover.</li>
        <li>Insert a t-nut (M5) inside the t-slot profile and position it in the lower part of the profile</li>
</table>

<table> <tr> <td>
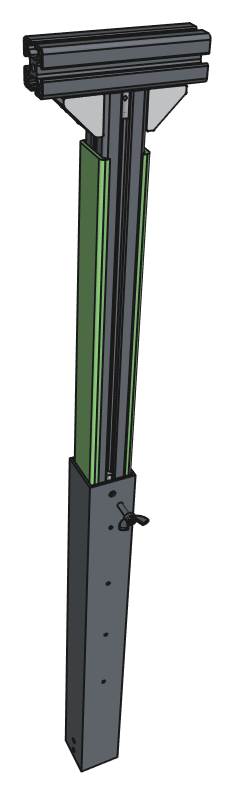
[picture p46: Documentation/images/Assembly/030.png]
         <br> 
</td> <td> <ul>
        <li>Insert the handlebar (top part) inside the handlebar (bottom part)</li>
        <li>It should slide in smoothly, but at the same time it should be relatively tight and not wobble</li>
        <li>If it doesn't fit right, use a deburrer to smooth the edges of the 3D-printed case slightly and try again</li>
</table>

<table> <tr> <td>
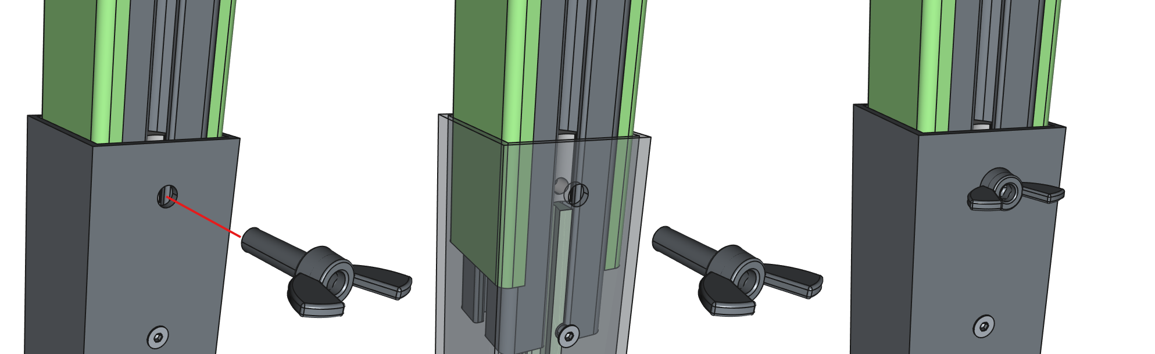
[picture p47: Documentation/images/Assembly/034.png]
         <br> 
</td> <td> <ul>
        <li>Insert an M5 x 16 wing screw in the top hole of the square tube</li>
        <li>Screw it into the t-nut</li>
</table>

<table> <tr> <td>
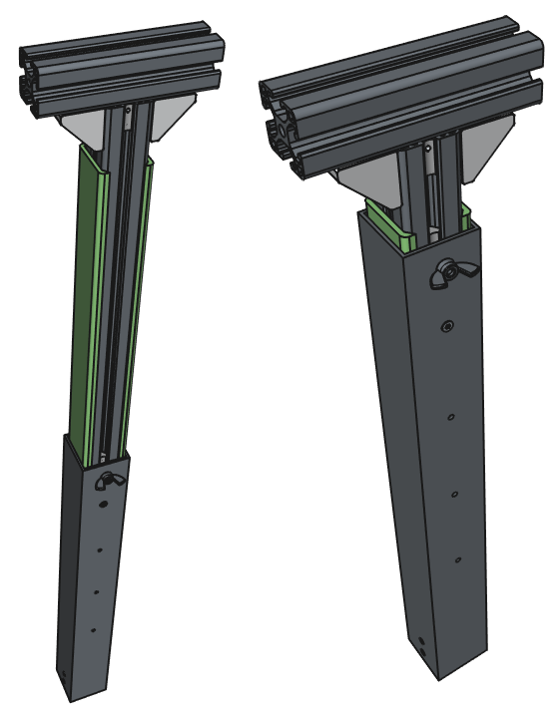
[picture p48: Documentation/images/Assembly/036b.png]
         <br> 
</td> <td> <ul>
        <li>Check whether you can adjust the height of the handlebars. <br> Loosen the wing screw, adjust the height, and then tighten the wing screw again.</li>
</table>

<table> <tr> <td>
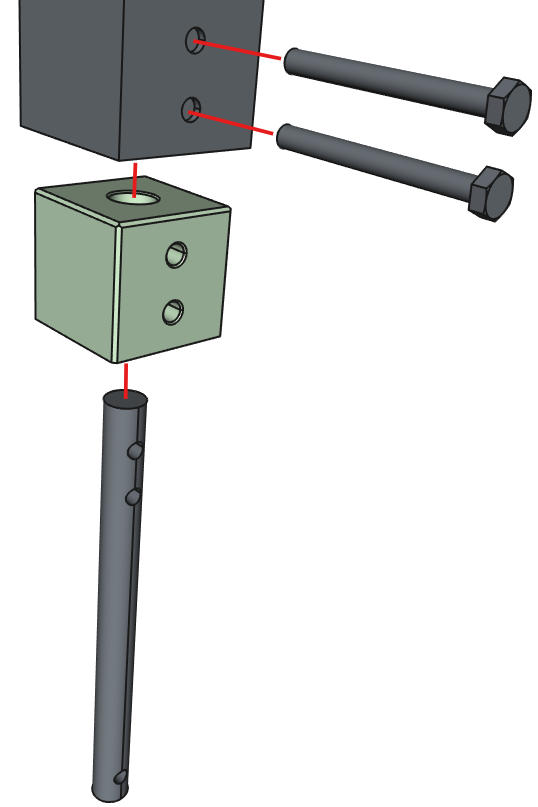
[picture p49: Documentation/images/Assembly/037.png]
         <br> 
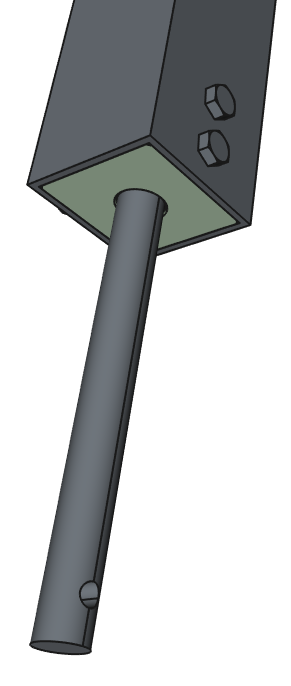
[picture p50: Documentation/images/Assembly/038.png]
        
</td> <td> <ul>
        <li>Insert the 3D-printed (nylon) connector in the bottom of the square tube</li>
        <li>Slide the axle (with the two holes at the top) into the 3D-printed connector</li>
        <li>Use two M5 x 50 screws with washers on each side (not shown in the images) to assamble the parts</li>
        <li>Use two M5 nuts to fasten the screws</li>
</table>

<table> <tr> <td>
         <br> 
</td> <td> <ul>
        <li>The handlebar (top and bottom part) is now fully assembled. Set it aside and continue with the assembly of the other modules.</li>
</table>

## 5. Bearing box

<table> <tr> <td>
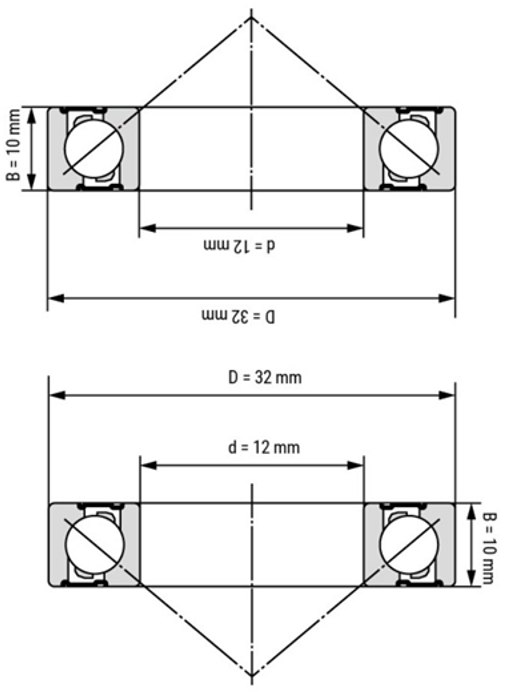
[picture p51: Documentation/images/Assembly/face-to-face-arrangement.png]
         <br> 
</td> <td> <ul>
        <li>Before we start assembling the bearing box, we need to unterstand how the <br> "angular contact ball bearings" (German "Schrägkugellager") work</li>
        <li>There are two ways to assamble a pair of angular contact ball bearings:</li>
                <ul>
                        <li>face-to-face arrangement (German "O-Anordnung")</li>
                        <li>back-to-back arrangement (German "X-Anordnung")</li>
                </ul>
        <li>For the orcuScooter, we want to use the face-to-face arrangement (see image)</li>
        <li>This means that the wide parts of the inner rings of the ball bearings must face outward, <br> while the narrow parts of the inner rings face inward</li>
        <li>When the ball bearings are inserted into the housings, the wide parts of the inner rings must be visible</li>
</table>

<table> <tr> <td>
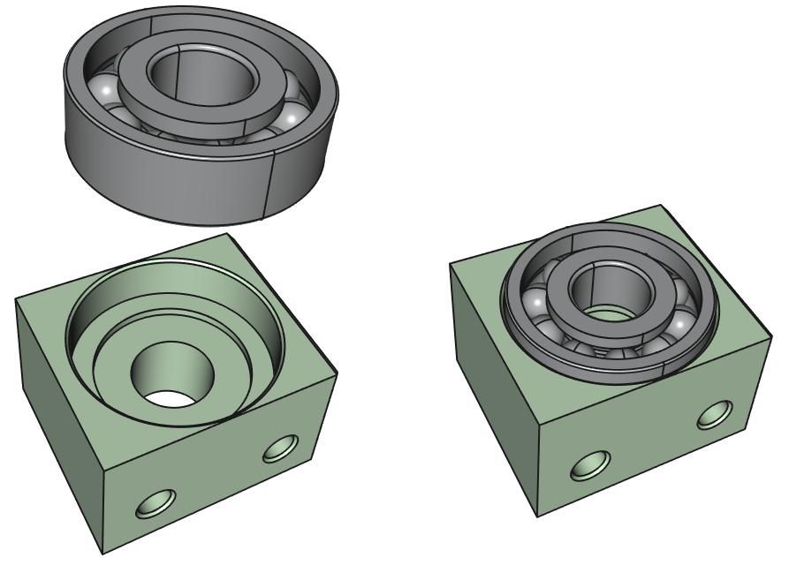
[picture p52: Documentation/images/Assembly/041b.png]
         <br> 
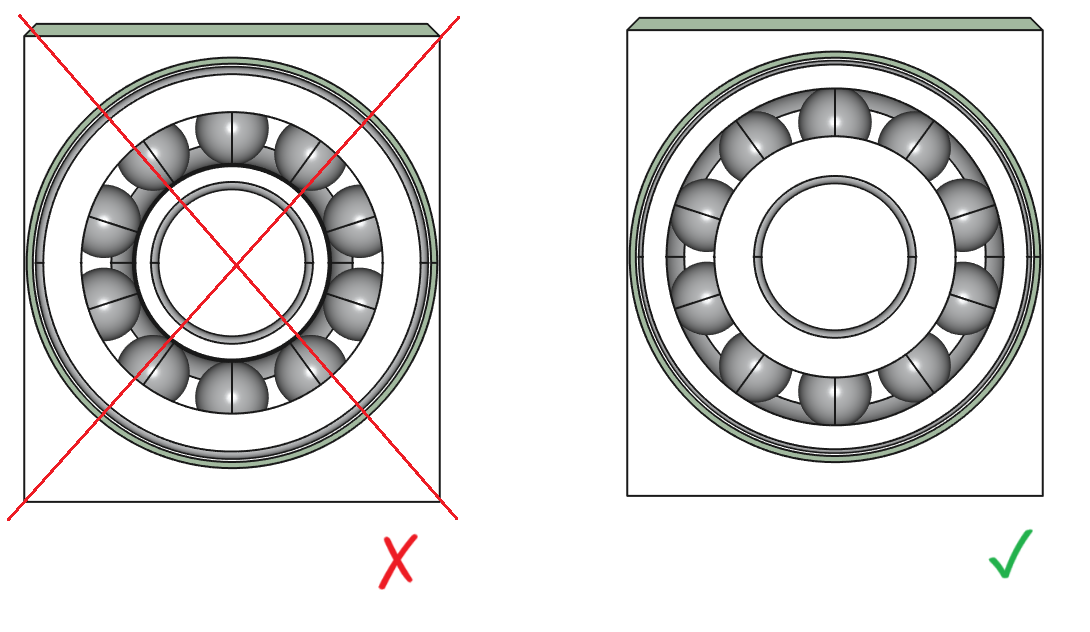
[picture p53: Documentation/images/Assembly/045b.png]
        
</td> <td> <ul>
        <li>Insert the ball bearings in the 3D-printed (nylon) bearing housings</li>
        <li>As mentioned above, the wide part of the inner ring must face outward</li>
        <li>The wide part of the inner ring must be visible, while the narrow part <br> is inside the housing (not visible)</li>
        <li>Assamble both bearing housings with the bearings the same way, <br> so you have two sets of identical bearing housings, each with a bearing inside</li>
</table>

<table> <tr> <td>
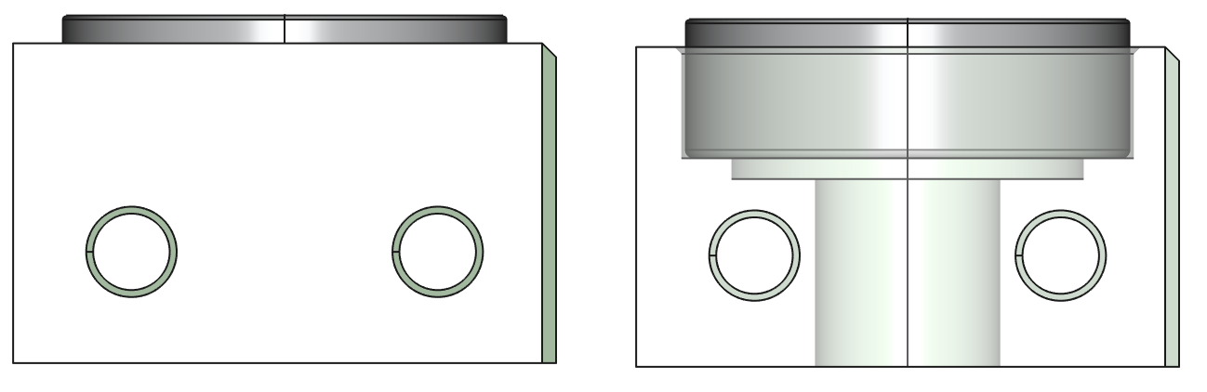
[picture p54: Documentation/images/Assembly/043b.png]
        
</td> <td> <ul>
        <li>Note that the bearings do not completely submerge <br> into the housings, but protrude approx. 2 mm.</li>
</table>

<table> <tr> <td>
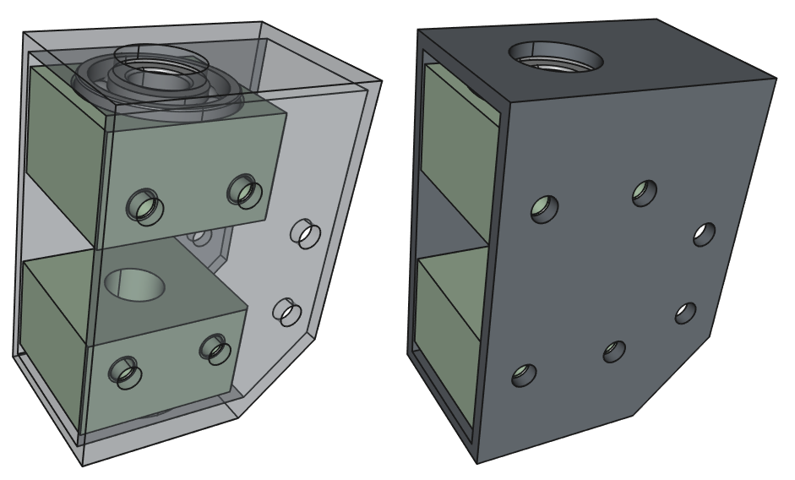
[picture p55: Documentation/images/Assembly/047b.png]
         <br> 
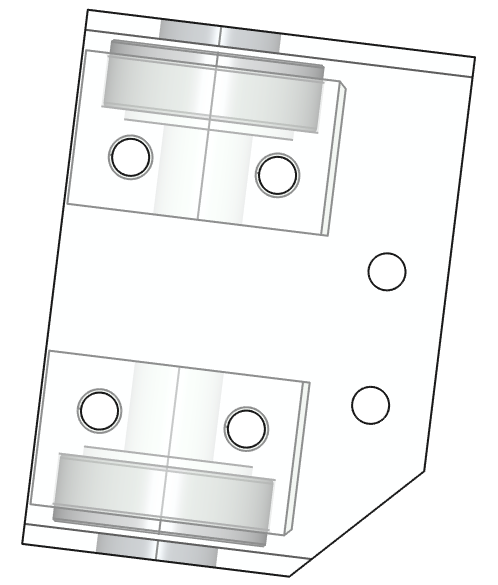
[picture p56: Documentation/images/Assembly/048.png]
         <br>
        
</td> <td> <ul>
        <li>Insert the housings with the bearings inside the aluminum bearing box</li>
        <li>Make sure that both bearings are facing outward (see image)</li>
        <li>Align the holes of the housings with the holes of the aluminum bearing box</li>
        <li>For each bearing box, use two M5 x 50 screws with washers on each side (not shown in the images)</li>
        <li>Fasten each of the 4 screws with an M5 nut (not shown in the images)</li>
</table>

<table> <tr> <td>
         <br> 
</td> <td> <ul>
        <li>The bearing box is now fully assembled. Set it aside and continue with the assembly of the other modules.</li>
</table>

## 6. Rear wheel

<table> <tr> <td>
         <br> 
        
</td> <td> <ul>
        <li>Before installing the rear wheel, insert four M5 t-nuts <br> in the frame (two on each side)</li>
        <li>You will need the t-nuts later for assembling the deck.</li>
        <li>Position the t-nuts as shown in the images. The exact <br> position can be corrected later when assembling the deck</li>
        <li>Make sure the two t-nuts in the back part are positioned <br> past the hole for the axle screw for the rear wheel</li>
</table>

<table> <tr> <td>
         <br> 
         <br>
        
</td> <td> <ul>
        <li>Prepare the following parts
                <ul>
                        <li>Rear wheel (diameter 120 mm)</li>
                        <li>2x 3D-printed spacers (11 x 8,5 mm)</li>
                        <li>M8 x 95 screw</li>
                        <li>M8 nut (not shown in the images)</li>
                        <li>2x washers (not shown in the images)</li>
                </ul>
        </li>
        <li>Have a pair of pliers ready that are narrow enough to insert the spacers.</li>
        <li>Put a washer on the screw</li>
        <li>Insert the screw through the hole (just a few millimeters beyond the hole)</li>
        <li>Put one of the spacers on the tip of the screw</li>
        <li>Hold the wheel and the other spacer (using the pliers) in position, then push the screw all the way through</li>
        <li>Put the second washer on the end of the screw and fasten it with an M8 nut</li>
        <li>Test the assembly. Make sure the wheel spins well and that it doesn't wobble.</li>
</table>

## Assembling the complete handlebar

<table> <tr> <td>
        
</td> <td> <ul>
        <li>Prepare the following modules and parts:</li>
          <ul>
                <li>assambled handle bar</li>
                <li>assambled bearing box</li>
                <li>3D-printed spacer (nylon) (17,4 x 6,5)</li>
          </ul>
        </li>
</table>

<table> <tr> <td>
        
</td> <td> <ul>
        <li>Put the spacer on the tip of the axle</li>
        <li>Push the axle with the spacer through the all the holes and both bearings in the bearing box</li>
</table>

<table> <tr> <td>
         <br>
        
</td> <td> <ul>
        <li>For the next step, it is important that the handlebar <br> and the fork (with the front wheel) are correctly <br> aligned with each other</li>
        <li>Rotate the upper part of the handlebar so that <br> the 3D-printed cover faces forward (note the <br> orientation of the bearing box at the bottom)</li>
        <li>The fork must now be installed so that the axle <br> with the front wheel is at the front (and not <br> at the rear, see images)</li>
        <li>This is important for stability while riding the scooter</li>
</table>

<table> <tr> <td>
         <br>
        
</td> <td> <ul>
        <li>Prepare the following modules and parts:</li>
          <ul>
                <li>assambled handle bar with the bearing box</li>
                <li>assambled fork with the front wheel</li>
                <li>3D-printed adapter (nylon)</li>
                <li>3D-printed spacer (nylon) (17,4 x 10)</li>
                <li>M5 x 50 screw</li>
                <li>2x washers</li>
                <li>M5 nut</li>
          </ul>
        <li>(1) Put the adapter inside the fork</li>
        <li>(2) Put the spacer on the tip of the axle, then push it <br> through the hole in the fork</li>
        <li>(3) Put a washer on the screw, then push the screw <br> through the hole</li>
        <li>Add another washer, then fasten the screw <br> with an M5 nut</li>
</table>

<table> <tr> <td>
        
</td> <td> <ul>
        <li>The handle bar with the bearing box and the front wheel fork is now fully assembled. Continue with the final assembly.</li>
</table>

## Add the safety bolt for the folding mechanism

<table> <tr> <td>
         <br>
         <br>
         <br>
        
</td> <td> <ul>
        <li>Assamble the safety bolt</li>
                  <ul>
                <li>Push the bolt (6 x 50 ) through the 3D-printed (PLA) lever part</li>
                <li>Screw the 3D-printed (PLA) cap on the lever part</li>
          </ul>
</table>

<table> <tr> <td>
         <br>
        
</td> <td> <ul>
        <li>Push the 3D-printed (PLA) bracket on the angle of the frame</li>
          </ul>
</table>

<table> <tr> <td>
         <br>
        
</td> <td> <ul>
        <li>Turn and position the cross connection so that the holes are aligned</li>
        <li>Push the bolt with the 3D-printed parts through all the holes</li>
          </ul>
</table>

<table> <tr> <td>
         <br>
        
</td> <td> <ul>
        <li>Turn the lever on the bolt into the bracket. This prevents the bolt from slipping out while riding the scooter.</li>
          </ul>
</table>

## Test the folding mechanism

<table> <tr> <td>
        
</td> <td> <ul>
        <li>Loosen the wing screw</li>
        <li>Push the handlebar down as far as it will go</li>
        <li>Tighten the wing screw again</li>
          </ul>
</table>

<table> <tr> <td>
         <br>
        
</td> <td> <ul>
        <li>Turn the lever to remove the safety bolt from the bracket</li>
        <li>Pull the safety bolt out</li>
        <li>Fold the scooter</li>
        <li>If everthing worked fine, fold the scooter back again and insert the safety bolt</li>
        <li>Turn the lever of the safety bolt back into the bracket</li>
          </ul>
</table>

## 🛴 Testing time!

The scooter is now ready for a first ride. Hop on, cruise to your heart's content and make sure everything is stable and sits right. If the scooter falls apart and you crash, there might be something wrong. Perhaps now is a good time to fix it, before you continue with the assembly.

But if the scooter has passed the test ride successfully: Well done! Continue with the instructions below.

## 7. Brake

<table> <tr> <td>
         <br>
         <br>
        
</td> <td> <ul>
        <li>Push the brake block into the brake part</li>
        <li>Note that the brake block has one slanted edge <br> and one straight edge. <br> Ensure correct alignment — the brake part also has these edges.</li>
          </ul>
</table>

<table> <tr> <td>
        
</td> <td> <ul>
        <li>If the brake block does not hold, you can use a rubber band (shown in yellow in the picture)</li>
        <li>If necessary, the rubber band must be wrapped twice</li>
          </ul>
</table>

<table> <tr> <td>
         <br>
         <br>
        
</td> <td> <ul>
        <li>Place the brake cover on the brake</li>
        <li>Use an M3 x 12 countersunk screw and an M3 nut to attach it</li>
          </ul>
</table>

<table> <tr> <td>
         <br>
         <br>
        
</td> <td> <ul>
        <li>Align the t-nuts in the frame with the holes of the brake</li>
        <li>Use two M5 x 10 countersunk screws to attach the brake to the t-nuts in the frame</li>
        <li>Make sure that the brake is centered</li>
          </ul>
</table>

<table> <tr> <td>
        
</td> <td> <ul>
        <li>Take a close look at the brake from the side. Make sure there is <br> a little gap between the brake block and the wheel</li>
        <li>Test: Spin the wheel quickly with your hand, then press the brake</li>
        <li>Take the scooter for another test ride. Don't ride too fast. <br> Step on the brake and test whether it works properly.</li>
        <li>⚠️ Careful! The brake could be stronger than you think. <br> If you ride too fast and step on the brake, you could come to a <br> really sudden stop, causing you to flip over the front.</li>
          </ul>
</table>

## 8. Handles

<table> <tr> <td>
         <br>
        
</td> <td> <ul>
        <li>Push the threaded rod (M5 x 123) through the hole in the handle bar</li>
        <li>Make sure the threaded rod is centered</li>
          </ul>
</table>

<table> <tr> <td>
         <br>
        
</td> <td> <ul>
        <li>Put a 3D-printed (PLA) handle adapter on the tip of the threaded rod</li>
        <li>Put an M5 nut into the pocket</li>
        <li>Screw the adapter together with the M5 nut on the threaded rod</li>
        <li>Do the same on the other side</li>
        <li>Tighten both adapters with the nuts</li>
          </ul>
</table>

<table> <tr> <td>
         <br>
        
</td> <td> <ul>
        <li>Push a handle into the adapter</li>
        <li>Fasten it with an M5 x 45 screw and an M5 nut</li>
        <li>Do the same with the second handle on the other side</li>
          </ul>
</table>

<table> <tr> <td>
        
</td> <td> <ul>
        <li>Both handles should be attached to the handle bar</li>
        <li>Try turning them and make sure they are tight</li>
          </ul>
</table>

## 9. Front cover

<table> <tr> <td>
        
</td> <td> <ul>
        <li>Make sure that the M3 T-slot nut on the back of the handlebar is aligned as shown in the image</li>
          </ul>
</table>

<table> <tr> <td>
         <br>
        
</td> <td> <ul>
        <li>Push the 3D-printed logo part into the <br> front cover part. Insert it from the inside.</li>
        <li>Push the front cover together with the <br> logo part onto the handlebar from above</li>
          </ul>
</table>

<table> <tr> <td>
        
</td> <td> <ul>
        <li>Use an M3 x 12 countersunk screw <br> to attach the cover part to the handlebar</li>
        <li>Screw it into the M3 T-slot nut</li>
          </ul>
</table>

## 10. Deck

<table> <tr> <td>
         <br>
         <br>
        
</td> <td> <ul>
        <li>Make sure that the M5 T-slot nuts are aligned as shown in the image</li>
        <li>Place the deck on the frame</li>
        <li>Use four M5 x 10 countersunk screws to mount the deck to the frame</li>
        <li>Screw them into the T-slot nuts</li>
          </ul>
</table>

## 🛴 Done!

<table> <tr> <td>
        
</td> <td> <ul>
        <li>That's it! The orcuScooter is fully assembled</li>
        <li>Take another test ride and make sure everything is working fine</li>
        <li>More upgrades and mods may follow in the future - stay tuned!</li>
        <li>Congrats on finishing the scooter, have fun and enjoy!</li>
          </ul>
</table>

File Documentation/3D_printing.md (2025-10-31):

# 3D printing

The STL files for 3D printing can be found [here](../3D_printing)

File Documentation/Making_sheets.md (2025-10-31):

# Making sheets from recycled plastics

A recycled plastic sheet measuring 530 x 530 x 6 mm is required for the orcuScooter project (sheets with similar thicknesses like 5-7 mm should work, too).

For more information about how to make a recycled plastic with Precious Plastic machines, see the [instructions in the orcuDispenser documentation](https://github.com/orcular-org/orcuDispenser/blob/main/Documentation/Making_sheets.md)

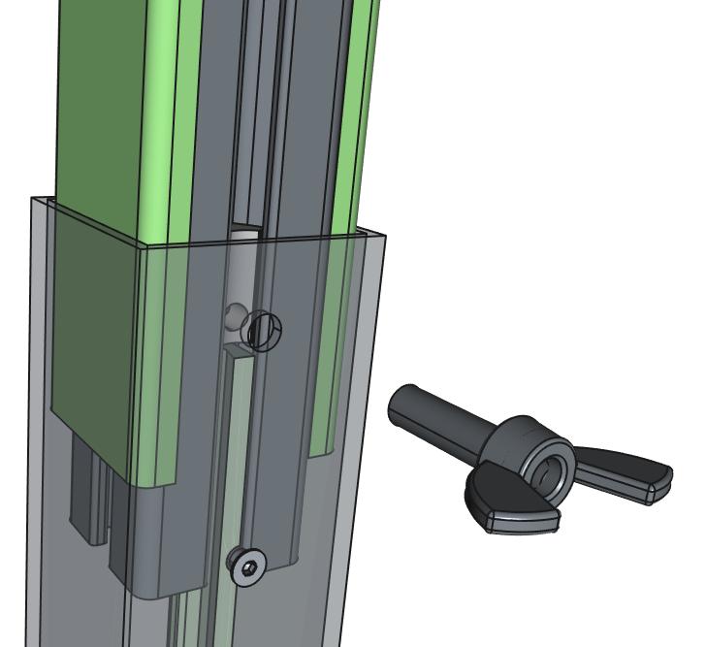
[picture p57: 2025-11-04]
Documentation/images/Assembly/032.png

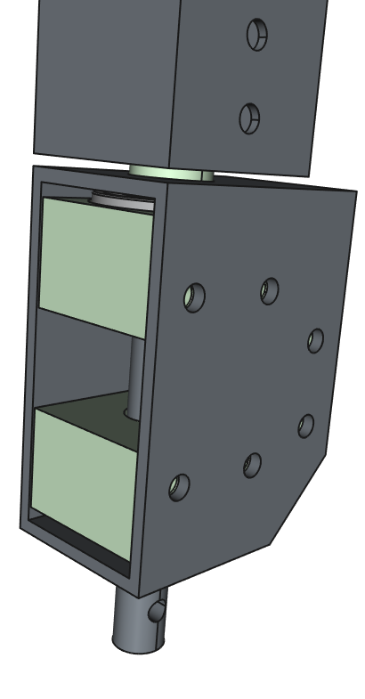
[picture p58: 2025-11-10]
Documentation/images/Assembly/064.png

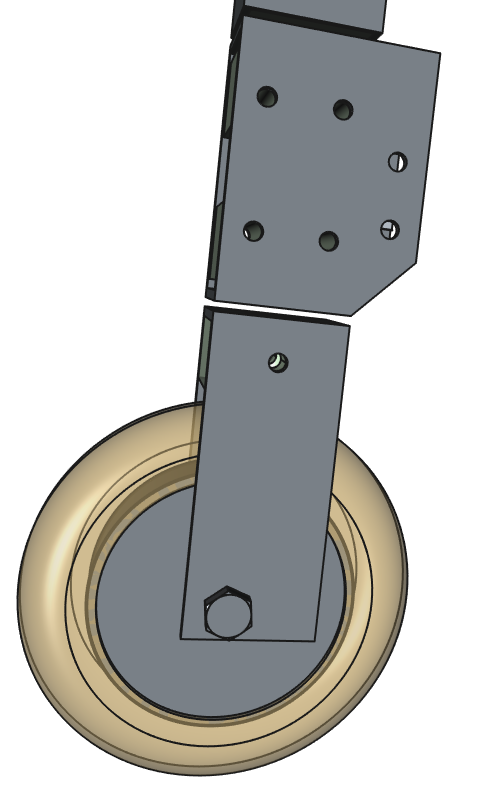
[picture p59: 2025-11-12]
Documentation/images/Assembly/087.png

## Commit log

2025-10-31 Add initial readme for CAD project
2025-10-31 Add README for 3D printing STL files
    Added information about the contents and usage of the folder.
2025-10-31 Add readme for CNC milling vector graphics files
2025-10-31 Create Shopping_list with BOM details
    Added a shopping list with a link to the BOM.
2025-10-31 Add BOM shopping list documentation
2025-10-31 Add 3D printing documentation
2025-10-31 Create Assembly.md with part and tool lists
    Added a new Assembly documentation file with part and tool lists.
2025-10-31 Fix link to Shopping_list.md in Assembly documentation
2025-10-31 Fix typo in Assembly.md for hexagon screws
2025-10-31 Enhance assembly instructions in Assembly.md
    Added detailed assembly instructions for the frame.
2025-10-31 Fix typo in assembly instructions
2025-10-31 Fix formatting and add assembly instructions
2025-10-31 Update assembly instructions and image reference
2025-10-31 Update assembly instructions in Assembly.md
    Added instructions for mounting angles and inserting screws.
2025-11-02 Fix grammar and clarity in Assembly.md
    Corrected grammatical errors and improved clarity in assembly instructions.
2025-11-02 Revise assembly instructions for front wheel and fork
    Updated assembly instructions for clarity and added missing parts.
2025-11-04 Add assembly instructions for handlebar components
2025-11-05 Fix typos and improve clarity in Assembly.md
2025-11-10 Fix spelling errors in Assembly documentation
    Corrected spelling of 'assembled' in multiple locations.
2025-11-10 Fix typo in safety bolt instructions
2025-11-12 Enhance assembly instructions with images and details
    Added images and instructions for handlebar and fork alignment during assembly.
2025-11-12 Document brake assembly and testing steps
    Added detailed instructions for brake assembly and testing.
2025-11-13 Add assembly instructions for the deck component
2025-11-14 Correct grammar in assembly instructions
